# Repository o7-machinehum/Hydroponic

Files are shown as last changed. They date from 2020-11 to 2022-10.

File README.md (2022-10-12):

# The Robotanist 
The Robotanist is a fully integrated and automated hydroponic rig. 

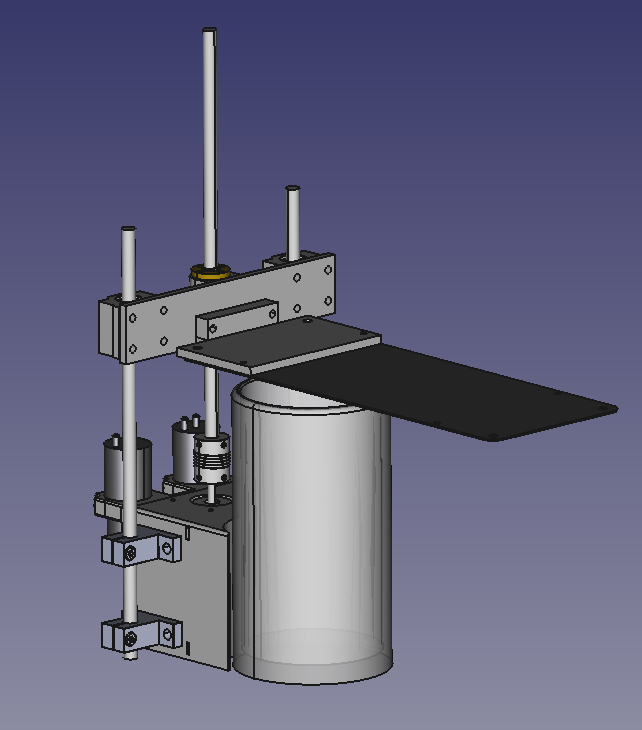
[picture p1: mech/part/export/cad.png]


Electronics
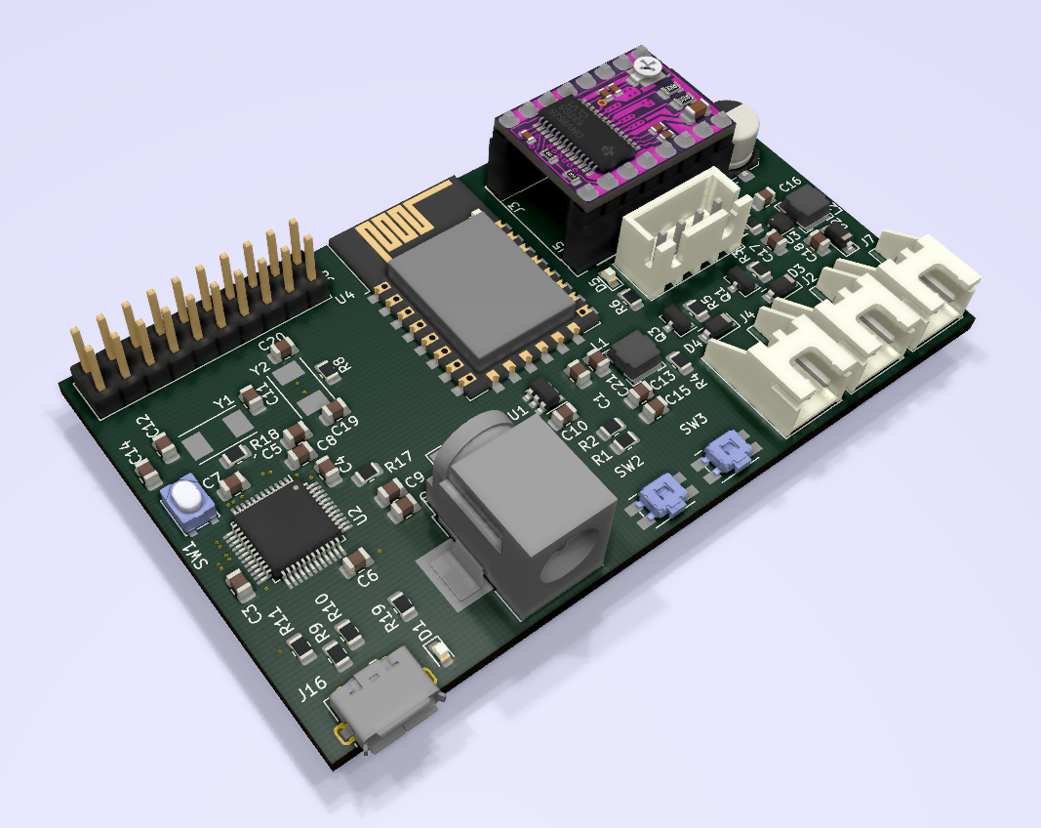
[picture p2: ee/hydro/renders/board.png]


Please find the electronics files in the ee folder, all pcb design is done with
the open source software KiCad. Is uses an STM32 as the main controller, and an
ST L6470 moter driver for the stepper motor. There are various connectors for
the subsystem components.

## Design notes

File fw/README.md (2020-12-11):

# Hydroponic Firmware
This is the folder that contains all the firmware for this project. It uses
gcc/make/openocd/gdb as the toolchain. It uses libopencm3 as the HAL and
FreeRTOS as the rtos.

## TODO
- PWM working

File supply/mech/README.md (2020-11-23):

# Ideaformer
Connie Wen - sales5@bell-ideaformer.com 
    2x NUT-ROD-T8P2L8-CP
    2x ROD-THR-T8P2L8-500
    4x ROD-SM-08-500
    8x SFSP-ROD-SM-SK8-SL
    4x LB-SC8UU-1
    2x CP-FLX-05081925
    - These are pretty much all the mech you need sans motors

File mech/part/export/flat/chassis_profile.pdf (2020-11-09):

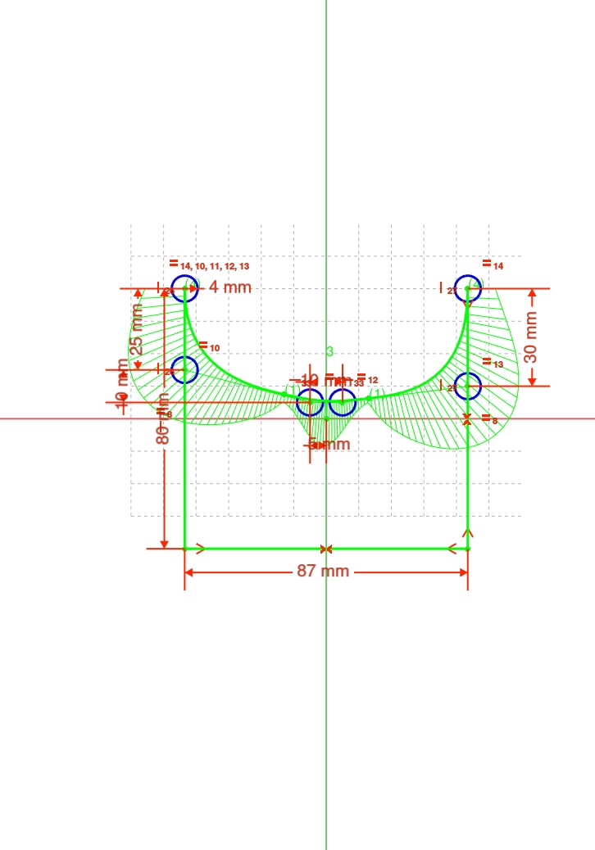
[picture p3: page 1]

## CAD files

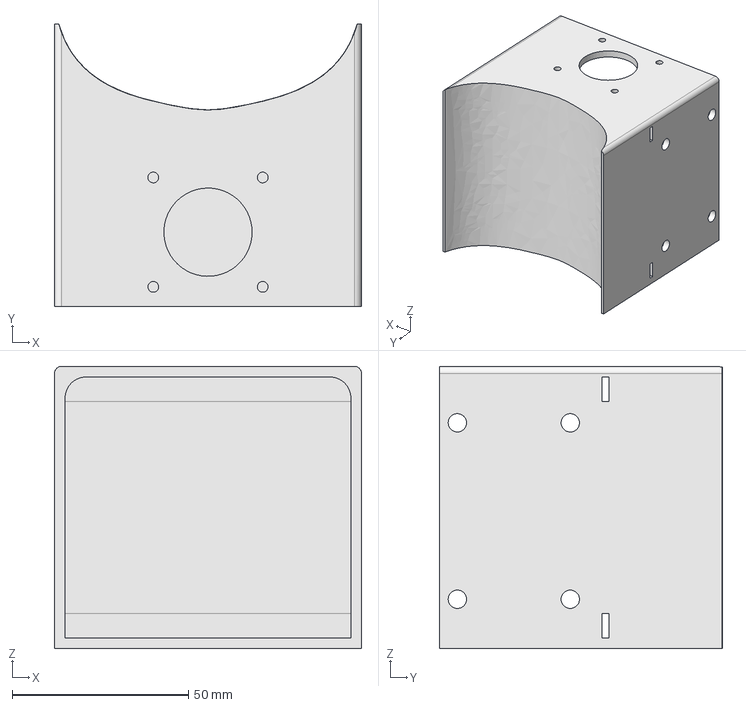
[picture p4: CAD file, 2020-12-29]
mech/asm.FCStd
87.0 x 80.1 x 80.0 mm

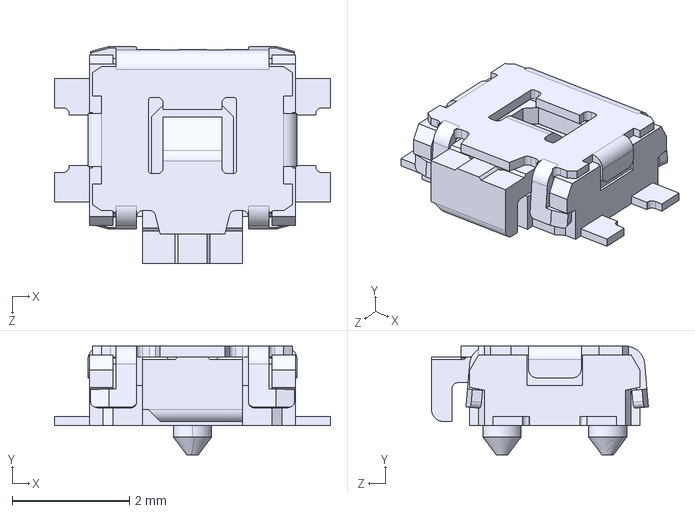
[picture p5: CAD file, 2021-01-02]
ee/hydro/3d/EVQP.step
4.70 x 1.85 x 3.69 mm

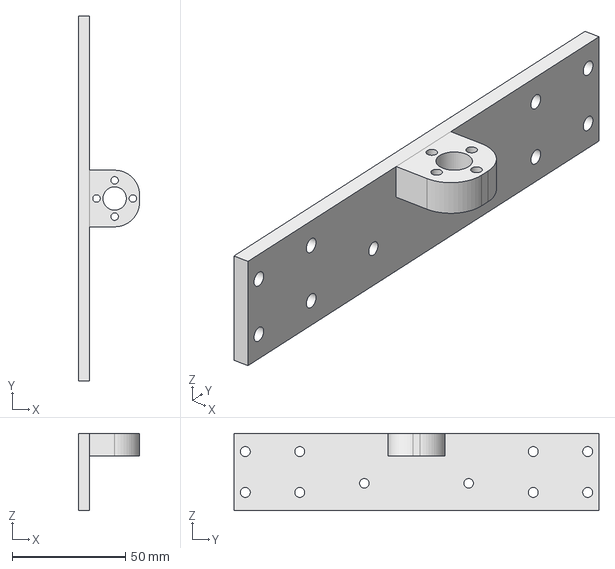
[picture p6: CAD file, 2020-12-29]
mech/led_carrier.FCStd
27.0 x 161.0 x 34.0 mm

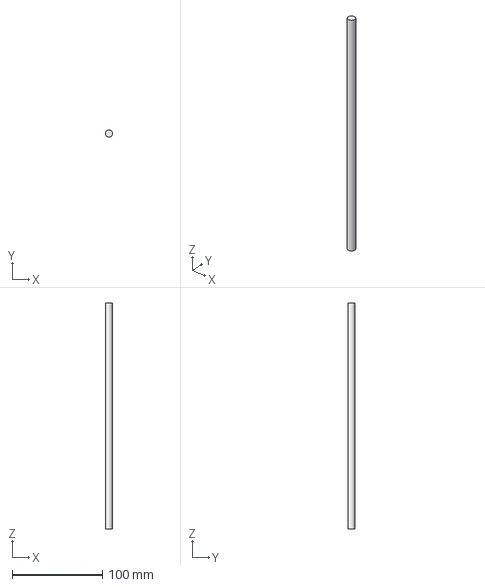
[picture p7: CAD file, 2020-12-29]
mech/part/500mm_Rail.FCStd
7.99 x 8.00 x 250.0 mm

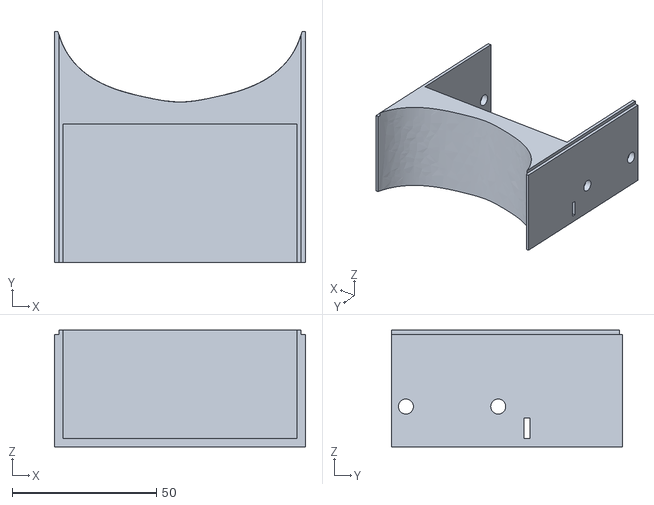
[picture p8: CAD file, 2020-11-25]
mech/part/export/chassis_bottom.stl
87.0 x 80.1 x 40.5

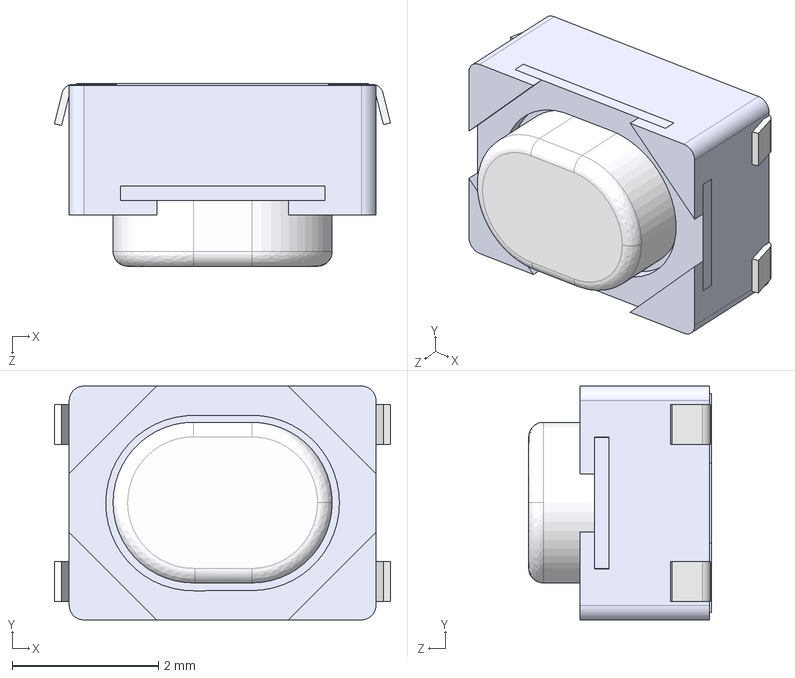
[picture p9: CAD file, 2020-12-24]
ee/hydro/3d/PTS810.step
4.60 x 3.20 x 2.50 mm
Strip
Button
Sheet Metal Part6 x 2
Pin

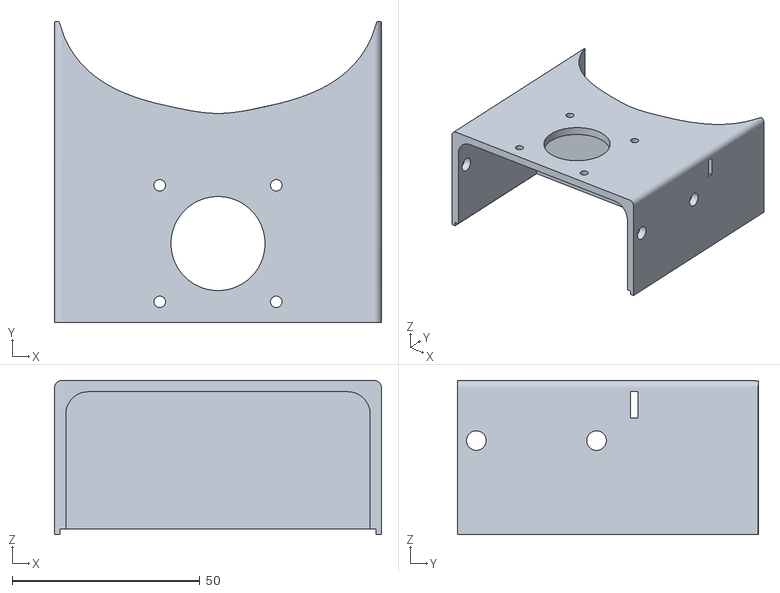
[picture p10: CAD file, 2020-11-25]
mech/part/export/chassis_top.stl
87.0 x 80.1 x 41.0

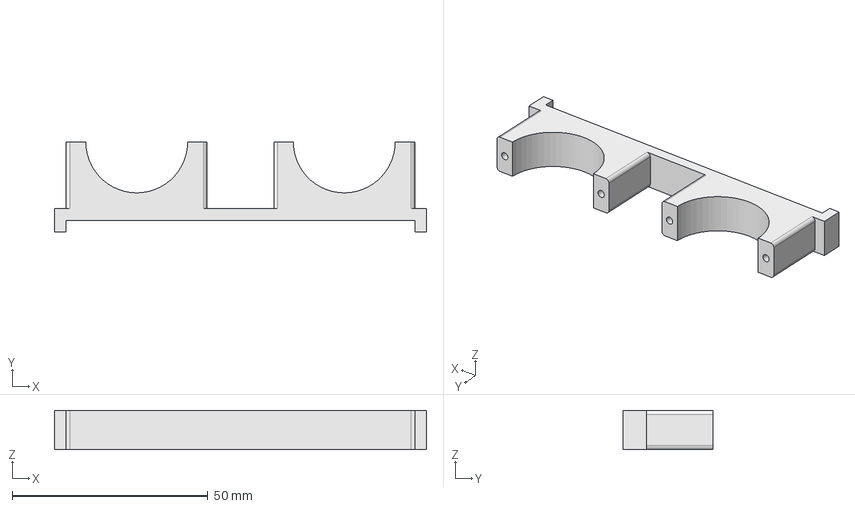
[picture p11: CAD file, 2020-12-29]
mech/part/pump_plate.FCStd
95.0 x 23.0 x 10.0 mm

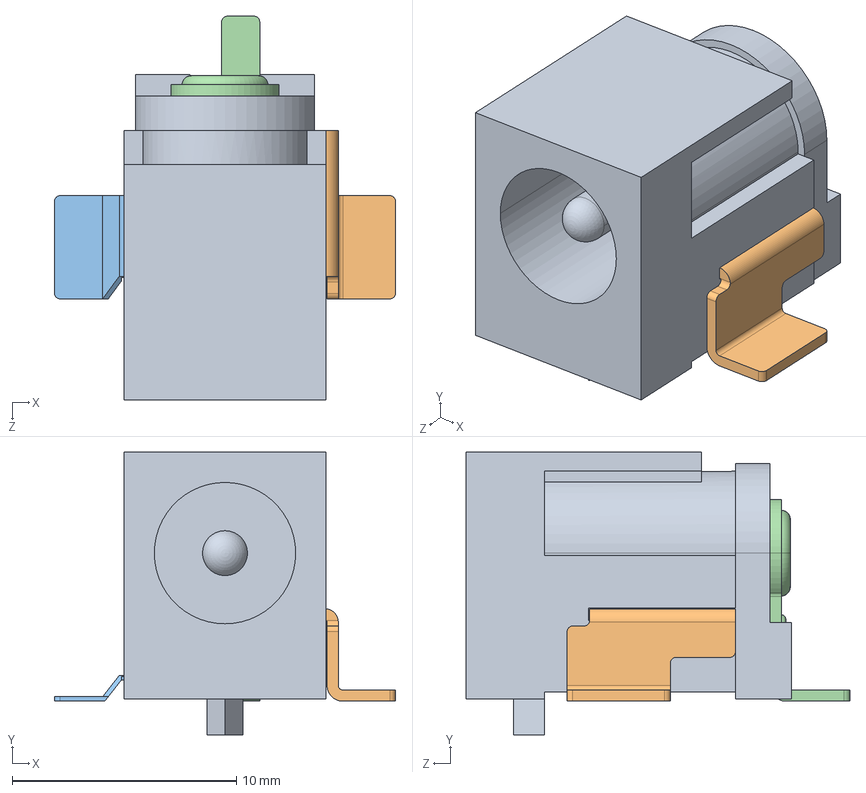
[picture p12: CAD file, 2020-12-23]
ee/hydro/3d/CUI_DEVICES_PJ-036AH-SMT-TR.step
15.2 x 12.6 x 17.1 mm

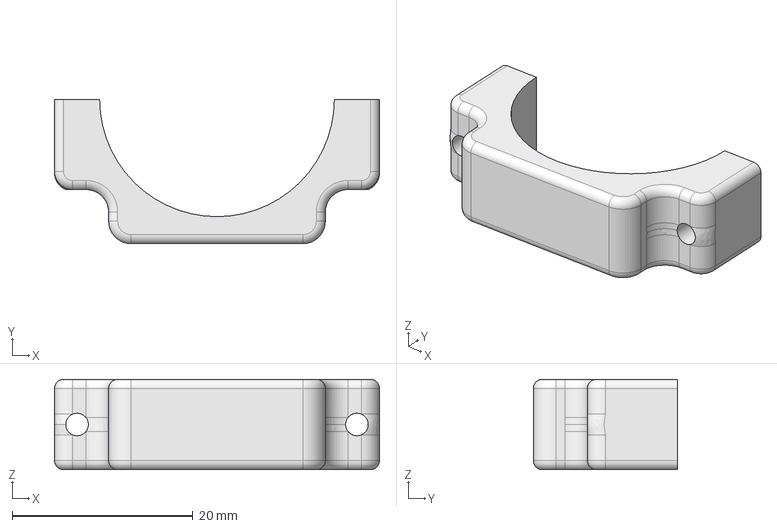
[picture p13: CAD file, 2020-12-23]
mech/part/pump_clamp.FCStd
36.0 x 16.0 x 10.0 mm

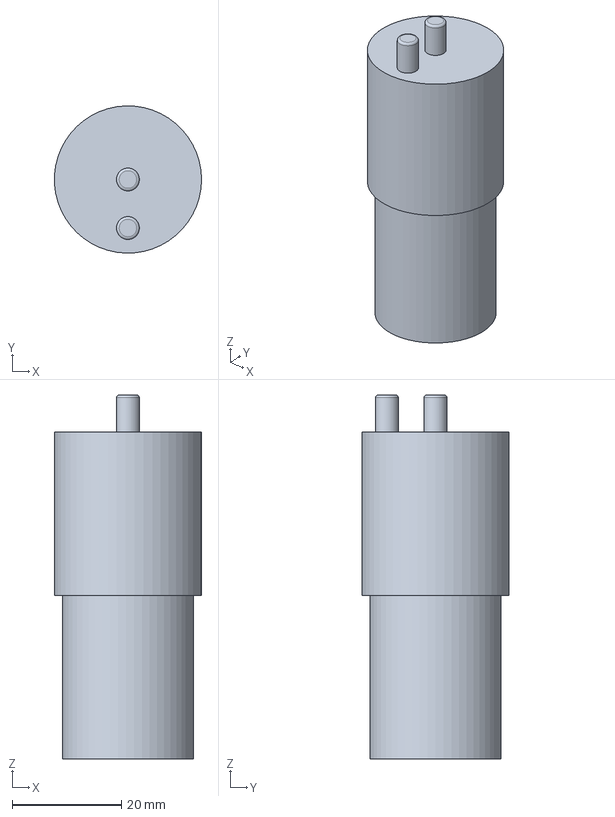
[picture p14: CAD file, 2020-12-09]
mech/part/12V_Pump.FCStd
27.0 x 27.0 x 66.8 mm

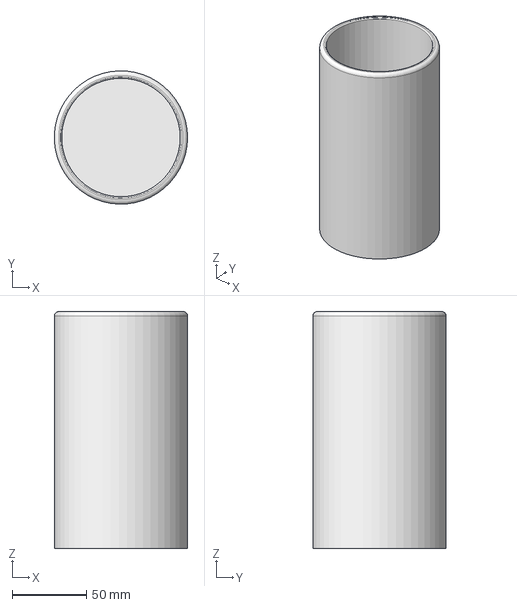
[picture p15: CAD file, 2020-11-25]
mech/part/jar.FCStd
89.9 x 90.0 x 160.0 mm

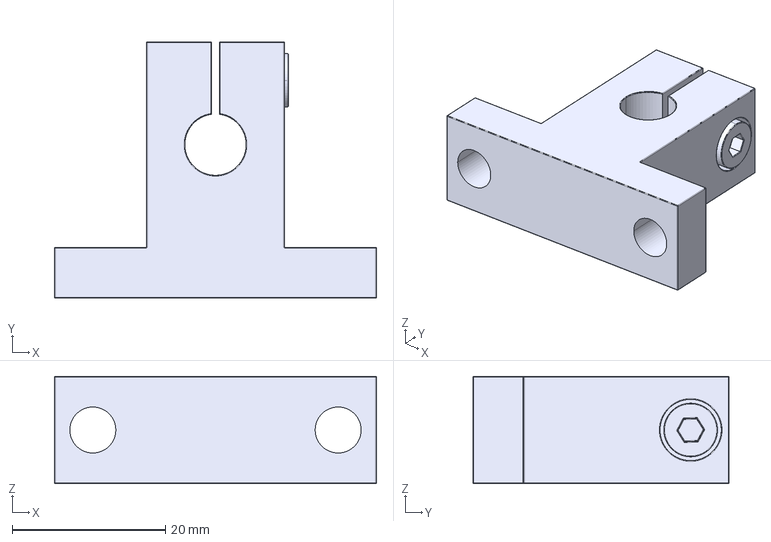
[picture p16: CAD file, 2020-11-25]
mech/part/sk8.FCStd
42.0 x 33.4 x 14.0 mm

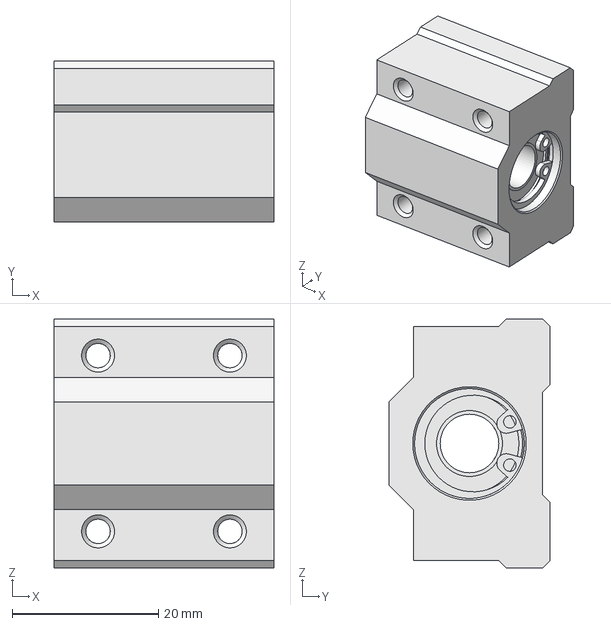
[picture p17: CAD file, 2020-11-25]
mech/part/SCS8UU.FCStd
30.0 x 22.0 x 34.0 mm

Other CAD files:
mech/part/led_panel.FCStd
mech/part/led_clamp.FCStd
mech/part/Nema17.FCStd
mech/part/D19L25.FCStd
ee/hydro/3d/475900001.stp
mech/part/Chassis.FCStd
mech/part/LED_Stand.FCStd
mech/part/Lead_Screw_Nut.FCStd
mech/part/Shaft_Support.FCStd
mech/part/export/led_carrier.stl
mech/part/export/led_clamp.stl
mech/part/export/pump_clamp.stl
mech/part/export/pump_plate.stl
mech/part/lead_screw.FCStd

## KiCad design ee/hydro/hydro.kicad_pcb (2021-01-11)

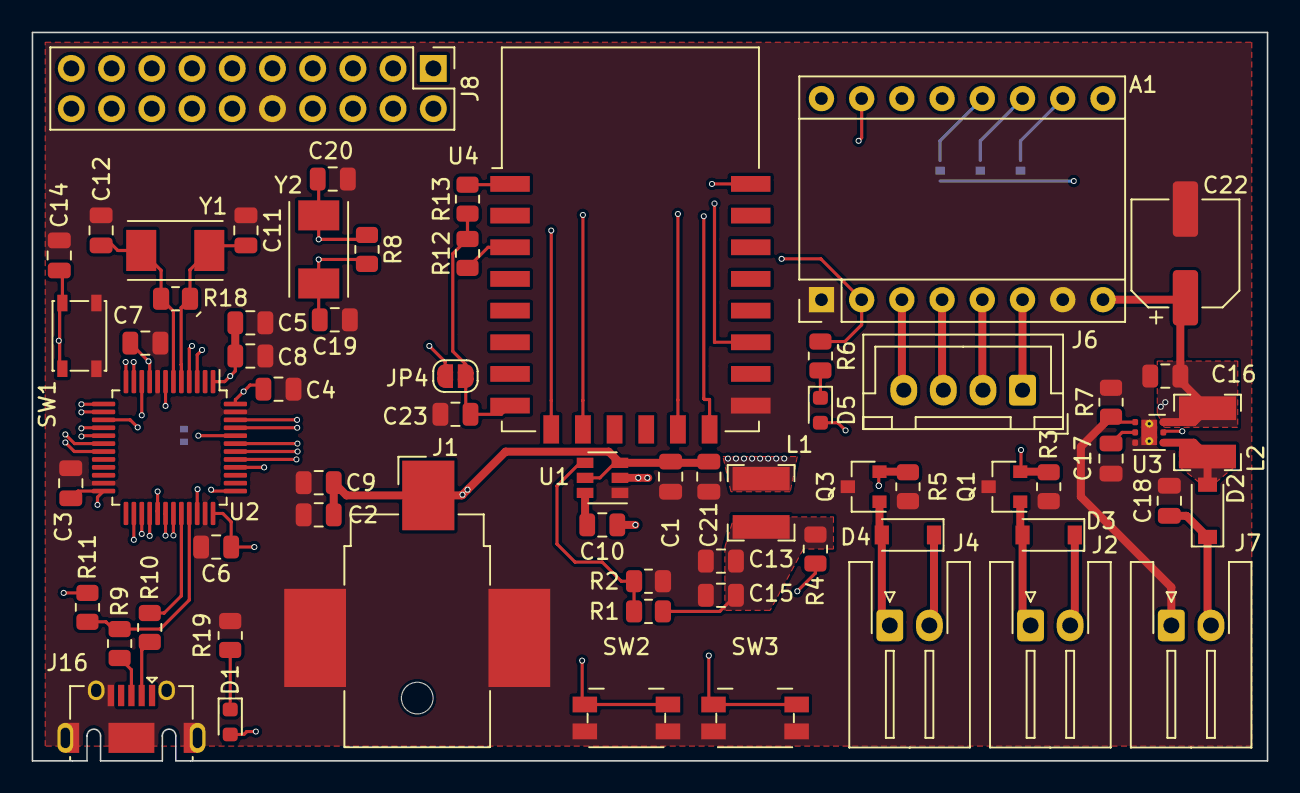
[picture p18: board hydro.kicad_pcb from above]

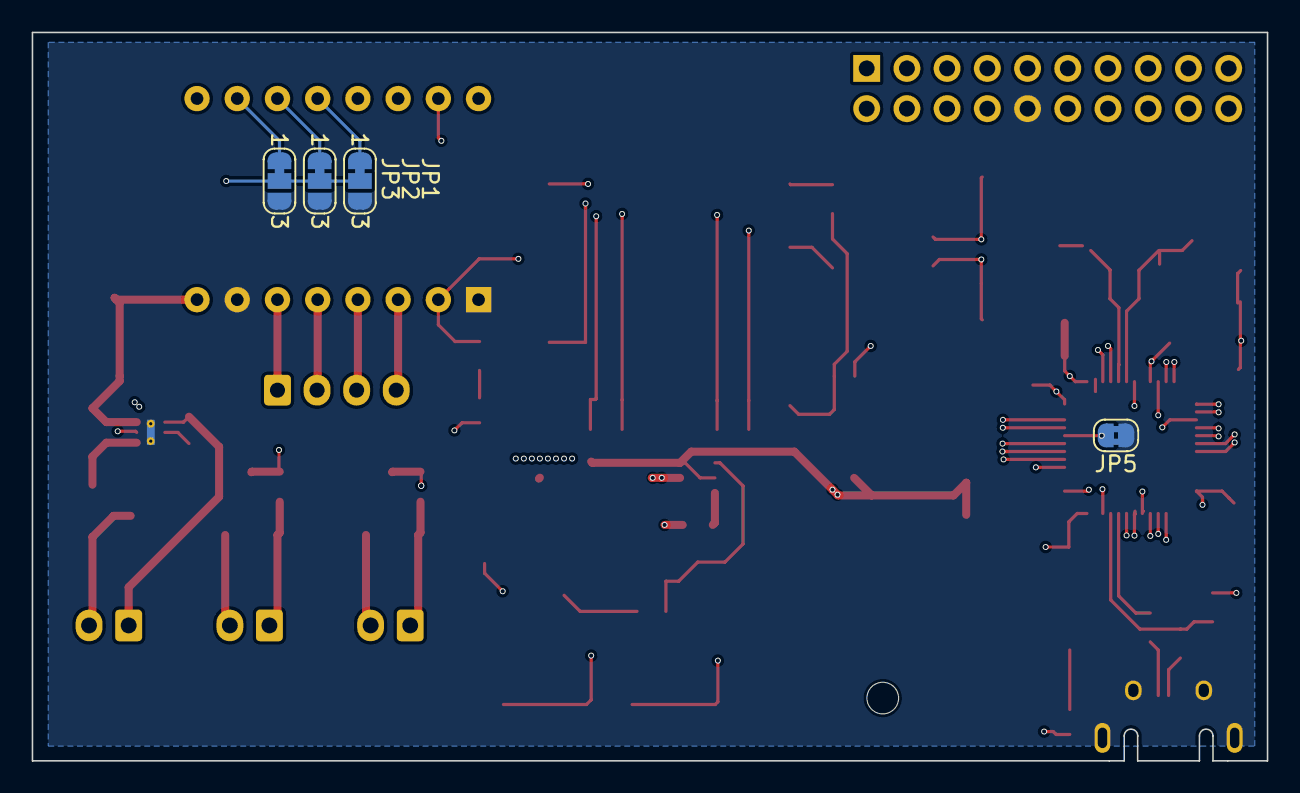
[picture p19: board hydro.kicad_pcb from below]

Board: 4 copper layers, 78.0 x 46.0 mm, 69 parts (4 on the bottom side), 65 nets.

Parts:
A1: DRV8825; Pololu_Breakout-16_15.2x20.3mm
C1, C13, C15: 22uF; C_0805_2012Metric
C2, C3, C9, C10: 10uF; C_0805_2012Metric
C4, C5, C6, C7, C8: 0.1uF; C_0805_2012Metric
C11, C12, C19, C20: 20pF; C_0805_2012Metric
C14, C16, C18, C21, C23: 1uF; C_0805_2012Metric
C17: 220nF; C_0805_2012Metric
C22: 100uF; CP_Elec_6.3x5.4
D1: LED Green; LED_0603_1608Metric
D2, D3, D4: MBR0540; D_SOD-123
D5: LED Red; LED_0603_1608Metric
J1: PJ-036AH-SMT-TR; BarrelJack_CUI_PJ-036AH-SMT_Horizontal
J2, J4, J7: Conn_01x02_Male; JST_XH_S2B-XH-A-1_1x02_P2.50mm_Horizontal
J6: Conn_01x04_Male; JST_XH_B4B-XH-A_1x04_P2.50mm_Vertical
J8: Conn_02x10_Counter_Clockwise; PinHeader_2x10_P2.54mm_Vertical
J16: USB_B_Micro; USB_Micro-AB_Molex_47590-0001
JP1, JP2, JP3: SolderJumper_3_Bridged12; SolderJumper-3_P1.3mm_Bridged12_RoundedPad1.0x1.5mm_NumberL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
JP4: Jumper_2_Open; SolderJumper-2_P1.3mm_Open_RoundedPad1.0x1.5mm
JP5: Jumper_2_Bridged; SolderJumper-2_P1.3mm_Bridged2Bar_RoundedPad1.0x1.5mm
L1: 3.3uH; L_Bourns-SRN4018
L2: 22uH; L_Bourns-SRN4018
Q1, Q3: DMP3099L-13; SOT-23
R1: 33.2k; R_0805_2012Metric
R2, R3, R5: 10k; R_0805_2012Metric
R4: 0R; R_0805_2012Metric
R6, R19: 1k; R_0805_2012Metric
R7: 10R; R_0805_2012Metric
R8, R12, R13, R18: 1M; R_0805_2012Metric
R9, R10: 20R; R_0805_2012Metric
R11: 1.5k; R_0805_2012Metric
SW1: Reset; SW_SPST_PTS810
SW2: Drain Tank; Panasonic_EVQPUJ_EVQPUA
SW3: Fill Tank; Panasonic_EVQPUJ_EVQPUA
U1: TPS562200DDCR; SOT-23-6
U2: STM32F103C8Tx; LQFP-48_7x7mm_P0.5mm
U3: TPS61161; WSON-6-1EP_2x2mm_P0.65mm_EP1x1.6mm_ThermalVias
U4: ESP-12E
Y1: 8Mhz; Crystal_SMD_Abracon_ABM7-2Pin_6.0x3.5mm
Y2: 32.768Khz; Crystal_SMD_Abracon_ABM7-2Pin_6.0x3.5mm

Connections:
+3V3: C3.1, C4.1, C5.1, C6.1, C7.1, C8.1, D5.2, J8.1, JP1.2, JP2.2, JP3.2, JP4.1, R4.2, R11.1, U2.1, U2.9, U2.24, U2.36, U2.48
+12V: A1.8, C1.1, C2.1, C9.1, C16.1, C21.1, C22.1, D3.1, D4.1, J1.1, J2.2, J4.2, L2.1, U1.3, U1.5, U3.6
/!RST: C14.1, SW1.1, U2.7
/Connector/LED_FB: J7.1, R7.1, U3.1
/Connector/LED_OUT: C18.1, D2.1, J7.2
/Connector/Mot_M0: A1.10, JP3.1
/Connector/Mot_M1: A1.11, JP2.1
/Connector/Mot_M2: A1.12, JP1.1
/Drain: SW2.1, U2.27
/ESP_CS0: J8.9, U4.9
/ESP_MISO: J8.8, U4.10
/ESP_MOSI: J8.7, U4.13
/ESP_RX: J8.5, U4.17
/ESP_SCLK: J8.6, U4.14
/ESP_TX: J8.4, U4.22
/Fill: SW3.1, U2.28
/LED: D1.2, U2.26
/Mot_Dir: A1.2, R6.1, U2.41
/Mot_En: A1.9, U2.40
/PA1: J8.14, U2.11
/PA2: J8.13, U2.12
/PA3: J8.16, U2.13
/PA4: J8.15, U2.14
/PA6: J8.18, U2.16
/PA7: J8.17, U2.17
/PB0: J8.19, U2.18
/PB1: J8.20, U2.19
/PB7: A1.13, U2.43
/PB8: A1.14, U2.45
/PB9: A1.16, U2.46
/Power/SW: C10.1, L1.2, U1.2
/Power/VBST: C10.2, U1.6
/Power/VFB: R1.2, R2.1, U1.4
/SWDCLK: J8.3, U2.37
/SWDIO: J8.2, U2.34
/TIM1_Pump1: Q1.2, R3.1, U2.10
/TIM2_LED: U2.29, U3.5
/TIM3_Pump2: Q3.2, R5.1, U2.15
/TIM4_Step: A1.15, U2.42
/UART1_RX: J8.11, U2.31
/UART1_TX: J8.12, U2.30
/USB_DM: R10.2, U2.32
/USB_DP: R9.2, R11.2, U2.33
GND: A1.1, A1.7, C1.2, C2.2, C3.2, C4.2, C5.2, C6.2, C7.2, C8.2, C9.2, C11.1, C12.1, C13.2, C14.2, C15.2, C16.2, C17.2, C18.2, C19.1, C20.1, C21.2, C22.2, C23.2, J1.2, J1.3, J8.10, J16.5, J16.6, JP1.3, JP2.3, JP3.3, JP5.1, Q1.3, Q3.3, R2.2, R3.2, R5.2, R7.2, R19.1, SW1.2, SW2.2, SW3.2, U1.1, U2.8, U2.23, U2.35, U2.47, U3.3, U3.7, U4.15
LF_OSC_IN: C19.2, R8.2, U2.3, Y2.1
LF_OSC_OUT: C20.2, R8.1, U2.4, Y2.2
unnamed: A1.3, J6.4
unnamed: A1.4, J6.3
unnamed: A1.5, J6.2
unnamed: A1.6, J6.1
unnamed: C13.1, C15.1, L1.1, R1.1, R4.1
unnamed: C17.1, U3.2
unnamed: D1.1, R19.2
unnamed: D2.2, L2.2, U3.4
unnamed: D3.2, J2.1, Q1.1
unnamed: D4.2, J4.1, Q3.1
unnamed: D5.1, R6.2
unnamed: J16.2, R10.1
unnamed: J16.3, R9.1
unnamed: JP5.2, U2.44
unnamed: R12.1, U4.3
unnamed: R13.1, U4.1
OSC_IN: C11.2, R18.2, U2.5, Y1.1
OSC_OUT: C12.2, R18.1, U2.6, Y1.2
VPP: C23.1, JP4.2, R12.2, R13.2, U4.8

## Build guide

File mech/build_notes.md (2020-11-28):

# Build Notes

## Main Assembly (asm)
- chassis_top/bottom.gcode 
    - Nema17 mounting holes 
        - M3 hole in part too tight. Was 3.05mm dia.
        - M3x6 screw good length
    - Motor allignment circle too large
    - SK8 mount
        - M5x16 works well. Need more

## LED Carrier Assembly (asm)
    - M3 Lead screw nut mounting holes too small. Moved from 3.1mm to 3.3
        - This should moved to a tapped hole in production

## Parts
    - SK8 will not immobilize the rail when tigntened down

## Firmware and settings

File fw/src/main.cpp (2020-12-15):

#include "FreeRTOS.h"
#include "task.h"

#include <libopencm3/stm32/rcc.h>
#include <libopencm3/stm32/flash.h>
#include <libopencm3/stm32/gpio.h>
#include <libopencm3/stm32/adc.h>
#include <libopencm3/stm32/timer.h>

#include "main.h"
#include "cli.h"
#include "hellocmd.h"
#include "pumpcmd.h"
#include "uart.h"
#include "pwm.h"

static void clock_setup(void)
{
    rcc_clock_setup_pll(&rcc_hse_configs[RCC_CLOCK_HSE8_72MHZ]);

    /* Enable GPIOA clock (for LED GPIOs). */
    rcc_periph_clock_enable(RCC_GPIOA);
    rcc_periph_clock_enable(RCC_GPIOB);
    rcc_periph_clock_enable(RCC_GPIOC);

    /* Enable clocks for GPIO port B (for GPIO_USART1_TX) and USART1. */
    rcc_periph_clock_enable(RCC_AFIO);
    rcc_periph_clock_enable(RCC_USART1);
    
    /* Timer clocks */
    rcc_periph_clock_enable(RCC_TIM1);
}

void test_task(void * parameters) {
    gpio_set_mode(GPIOC, GPIO_MODE_OUTPUT_2_MHZ,
    GPIO_CNF_OUTPUT_PUSHPULL, GPIO13);

    while(true){
        vTaskDelay(10);
        gpio_toggle(GPIOC, GPIO13);
    }
}

void cli_task(void * parameters) {
    auto cli = (CLI *) parameters; 
    
    // Run the CLI
    cli->present();
}

int main(void) {
    clock_setup();
    uart* uart1 = new uart();

    pwm* pump1  = new pwm(GPIOA, GPIO8, TIM1, 1e4, 0.99, CLOCK);
    pwm* pump2  = new pwm(GPIOA, GPIO0, TIM2, 1e4, 0.99, CLOCK);

    pump1->start();

    Cmd* menu[] = {
        new HelloCmd("hello", uart1),
        new PumpCmd("pump", uart1, pump1, pump2),
        0
    };

    CLI* cli = new CLI("CMD> ", uart1, menu);

    // xTaskCreate(test_task,"demo", 128, NULL, 1, NULL);
    xTaskCreate(cli_task, "cli" , 128, cli, 1, NULL);
    vTaskStartScheduler();

    while(true);
    
}

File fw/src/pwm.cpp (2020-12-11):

#include "pwm.h"
#include <libopencm3/stm32/rcc.h>
#include <libopencm3/stm32/gpio.h>
#include <libopencm3/stm32/timer.h>

// Period in uS
pwm::pwm(uint32_t port, uint16_t pin, uint32_t tim, uint32_t freq, float duc, uint32_t sysclk) 
: tim(tim), freq(freq), clk(sysclk)
{
    rcc_periph_clock_enable(RCC_AFIO);
    gpio_set_mode(port, GPIO_MODE_OUTPUT_50_MHZ, GPIO_CNF_OUTPUT_ALTFN_PUSHPULL, pin);

    timer_set_mode(tim, TIM_CR1_CKD_CK_INT, TIM_CR1_CMS_CENTER_1,
                   TIM_CR1_DIR_UP);

    timer_set_oc_mode(tim, TIM_OC1, TIM_OCM_PWM2);
    timer_enable_oc_output(tim, TIM_OC1);
    timer_enable_break_main_output(tim);

    set_duc(duc);
    set_freq(freq);
}

pwm::~pwm() {
    stop();
}

// pec duc
void pwm::set_duc(float duc) {
    timer_set_oc_value(tim, TIM_OC1, uint32_t((1-duc)*freq_to_ticks(freq)));
}

void pwm::set_freq(uint32_t f) {
    freq = f;
    timer_set_period(tim, freq_to_ticks(f));
}

void pwm::start() {
    timer_enable_counter(tim);
}

void pwm::stop() {
    timer_disable_counter(tim);
}

uint32_t pwm::freq_to_ticks(uint32_t f) {
    return uint32_t(clk / (freq*2));
}

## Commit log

2020-11-09 Initial commit. All parts fine with FreeCAD 0.18
    [500mm_Rail.FCStd, Chassis.FCStd, LED_Stand.FCStd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]
2020-11-16 Added all the parts
    [500mm_Rail.FCStd, Chassis.FCStd, Lead_Screw_Nut.FCStd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]
2020-11-23 Mech is looking good, added some supply documents and emails.
    [500mm_Rail.FCStd, D19L25.FCStd, Nema17.FCStd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]
2020-11-25 Working away on the mech. Split the main assembly into two pieces
    [500mm_Rail.FCStd, LED_Stand.stl, SCS8UU.FCStd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]
2020-11-25 Left some parts behind
    [chassis_bottom.stl, chassis_top.stl, jar.FCStd]
2020-11-26 Generate some new parts. Couple of changed in the assembly.
    [500mm_Rail.FCStd, asm.FCStd, led_carrier.FCStd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]
2020-11-28 Working on the mech, changed some hole sizes
    [500mm_Rail.FCStd, asm.FCStd, led_carrier.FCStd]
2020-12-03 Ripped out the cube shit, going with libopencm3
    [500mm_Rail.FCStd, asm.FCStd, led_carrier.FCStd]
2020-12-07 Uart plummed into the CLI
2020-12-09 Added readme, added pump clamps
    [12V_Pump.FCStd, 500mm_Rail.FCStd, asm.FCStd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]
2020-12-11 Added pump stl files and gcode.
    [pump_clamp.stl, pump_plate.stl]
2020-12-11 pwm classes built, need to clean up the warnings
2020-12-11 PWM freq & DUC working fine
2020-12-11 Moved the clock start outta the pwm class
2020-12-23 Working on the PCB
    [475900001.stp, CUI_DEVICES_PJ-036AH-SMT-TR.step, Connector.sch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]
2020-12-23 Working on the mech
    [asm.FCStd, pump_clamp.FCStd, pump_plate.FCStd]
2020-12-23 Added the color sensor
2020-12-24 Working on the board, parts are in place. Need som mounting holes.
    [Connector.sch, PTS810.step, Power.sch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]
2020-12-29 Unknown changes
    [500mm_Rail.FCStd, asm.FCStd, led_carrier.FCStd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]
2021-01-02 Working on the ee parts of the design, placed two switches for fill and drain. Moved around some parts.
    [Connector.sch, EVQP.step, Power.sch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]
2021-01-07 Routing out the pins for the MCU
    [hydro.kicad_pcb, hydro.sch]
2021-01-07 Working on the board
    [Connector.sch, hydro.kicad_pcb, hydro.sch]
2021-01-11 Routing "finished", building a master todo list now.
    [Connector.sch, Power.sch, hydro.kicad_pcb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]
